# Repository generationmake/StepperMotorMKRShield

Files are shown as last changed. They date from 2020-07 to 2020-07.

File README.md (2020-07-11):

# StepperMotorMKRShield
StepperMotorMKRShield with Trinamic TMC5130A-TA drivers for two stepper motors compatible with Arduino MKR 

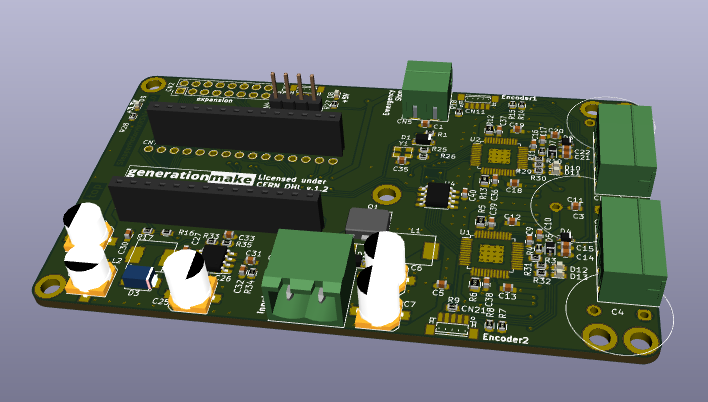
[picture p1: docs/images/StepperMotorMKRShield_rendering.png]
StepperMotorMKRShield rendering


## PCB

### Top

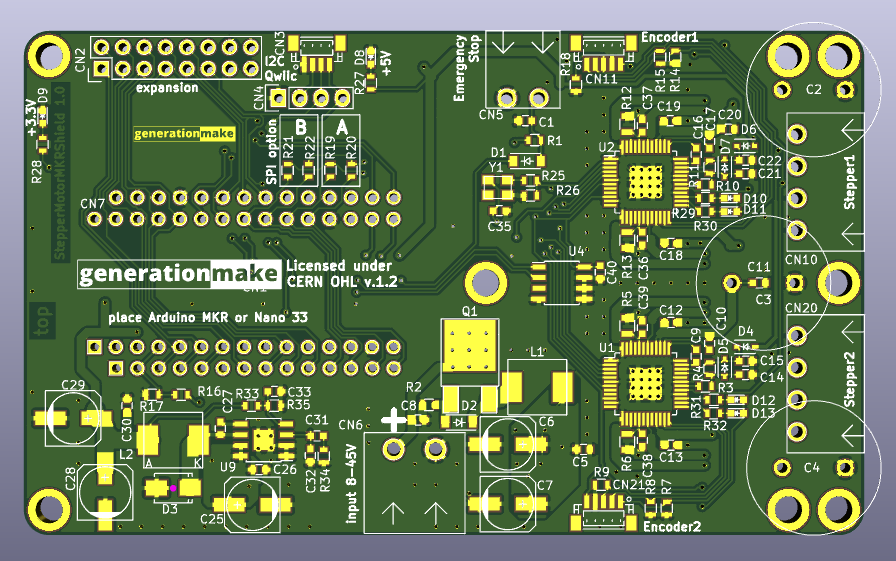
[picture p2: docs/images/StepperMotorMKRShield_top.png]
StepperMotorMKRShield PCB top


### Bottom

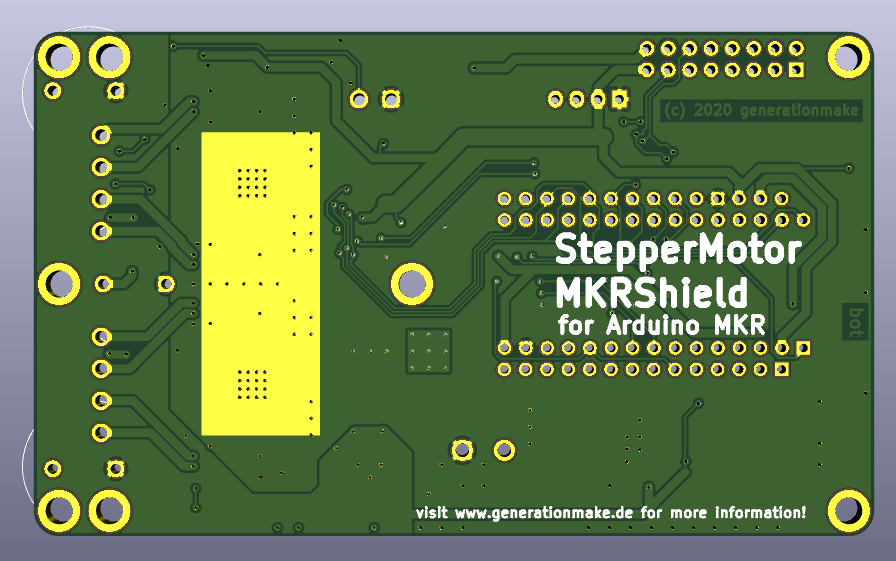
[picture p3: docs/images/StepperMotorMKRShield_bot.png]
StepperMotorMKRShield PCB bot


## License

This hardware is licensed under the CERN OHL v. 1.2

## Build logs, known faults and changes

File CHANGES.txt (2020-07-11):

StepperMotorMKRShield - Stepper Motor driver feather wing for Arduino MKR
see full project documentation at https://github.com/generationmake/StepperMotorMKRShield

changes

version 1.0 - 2020-07-12
* initial release

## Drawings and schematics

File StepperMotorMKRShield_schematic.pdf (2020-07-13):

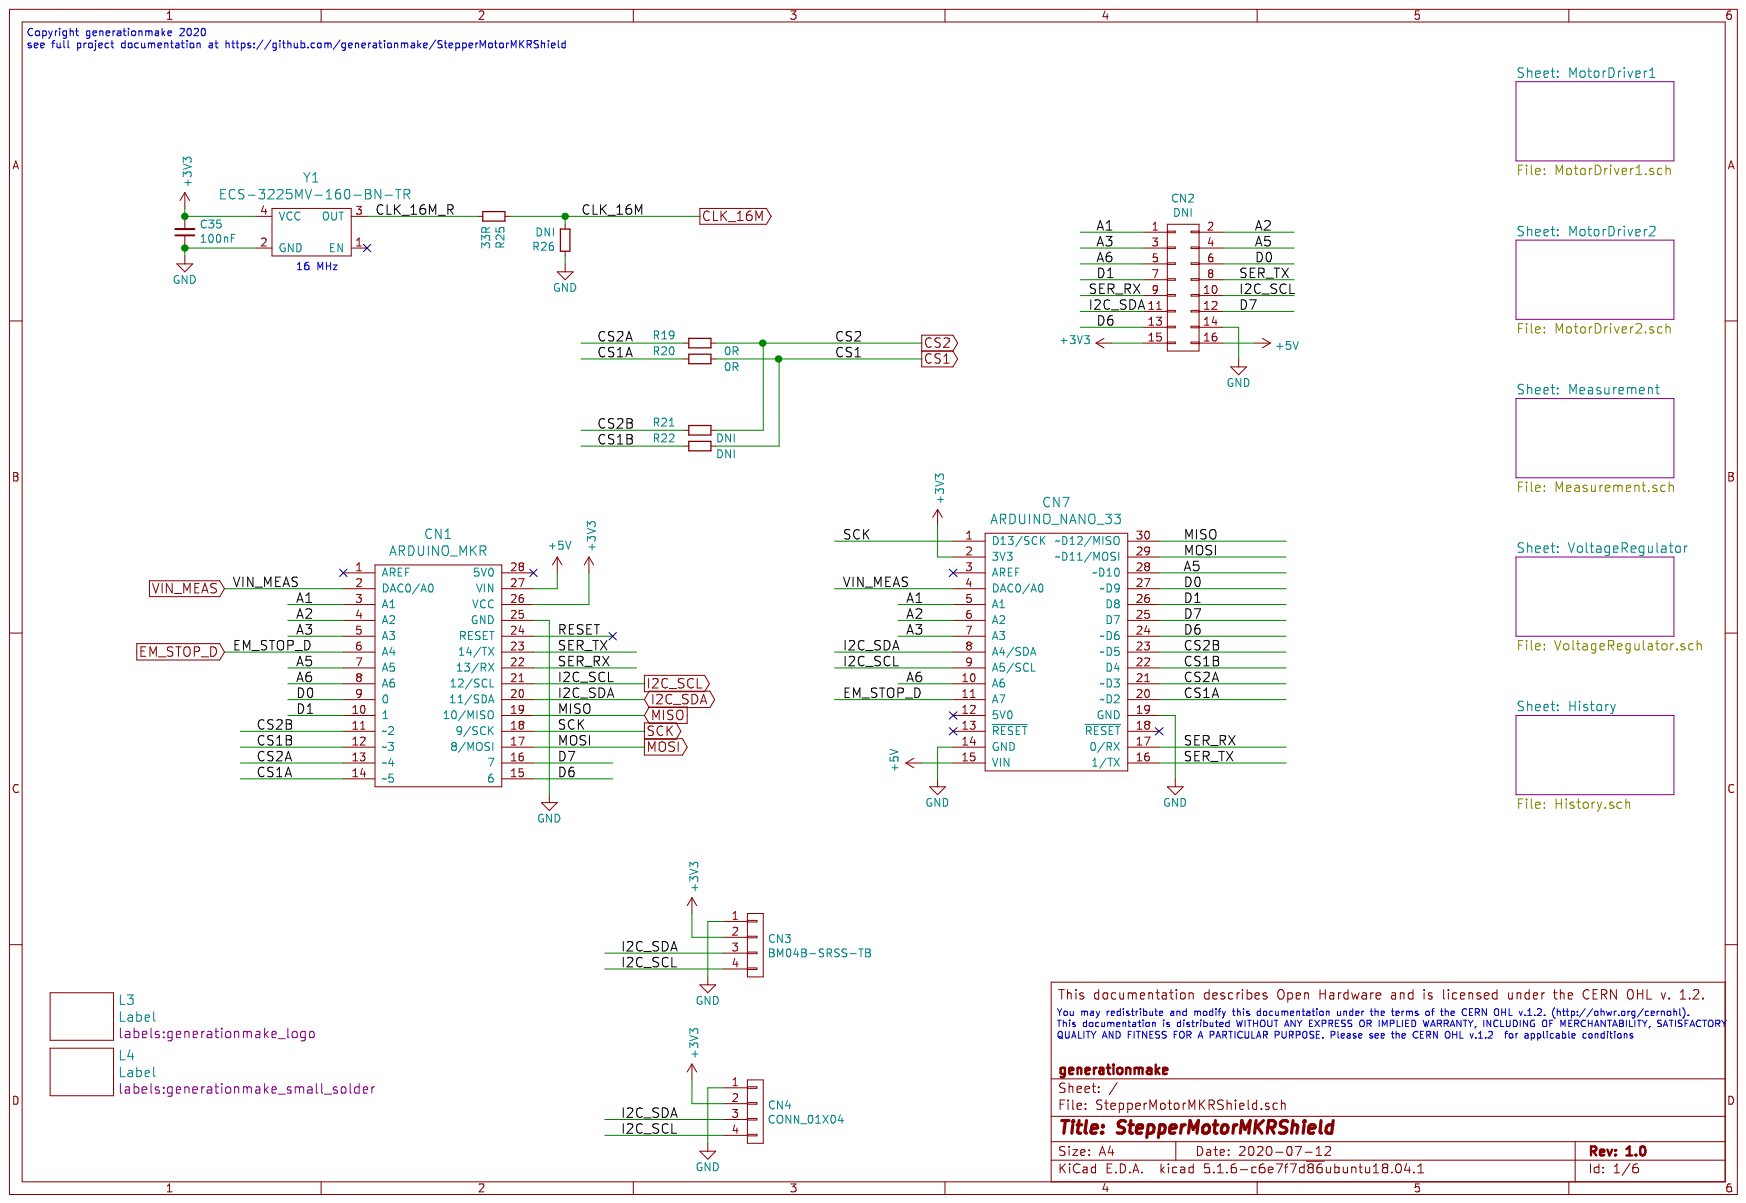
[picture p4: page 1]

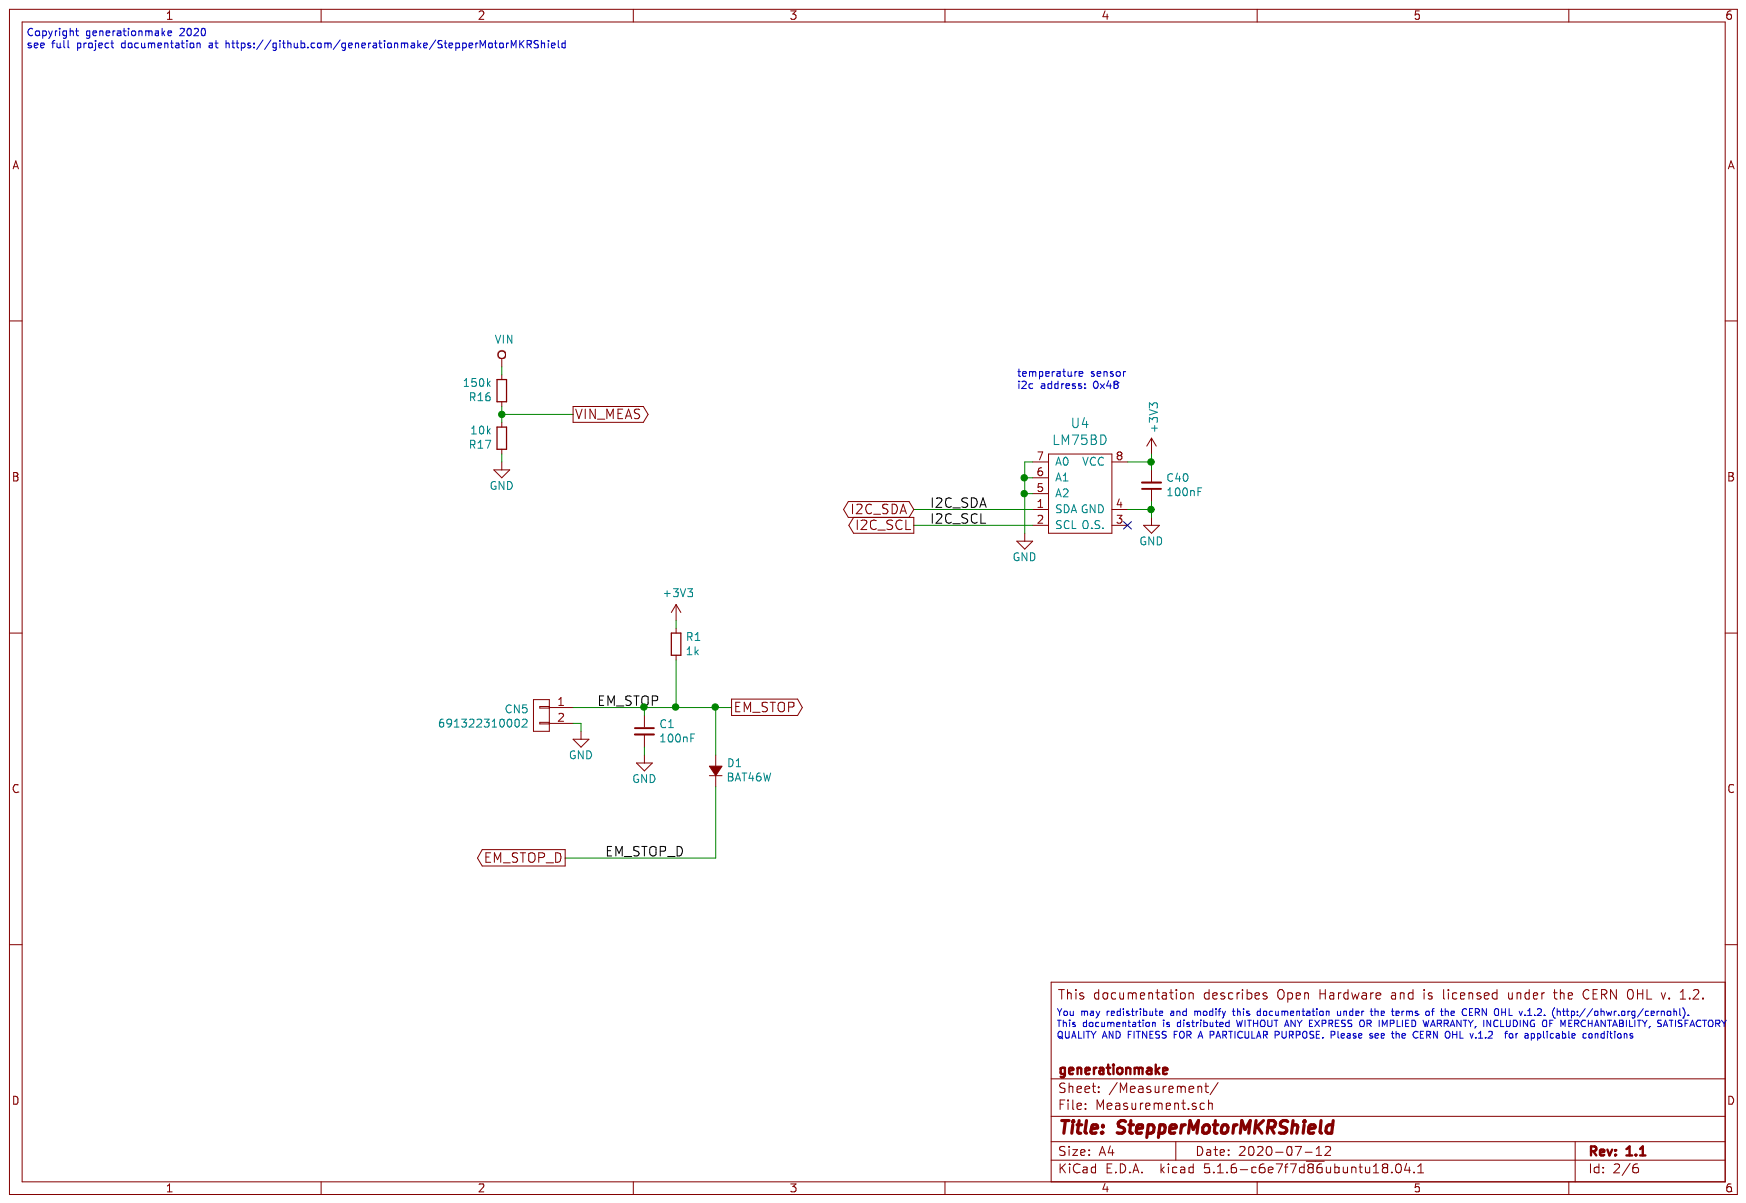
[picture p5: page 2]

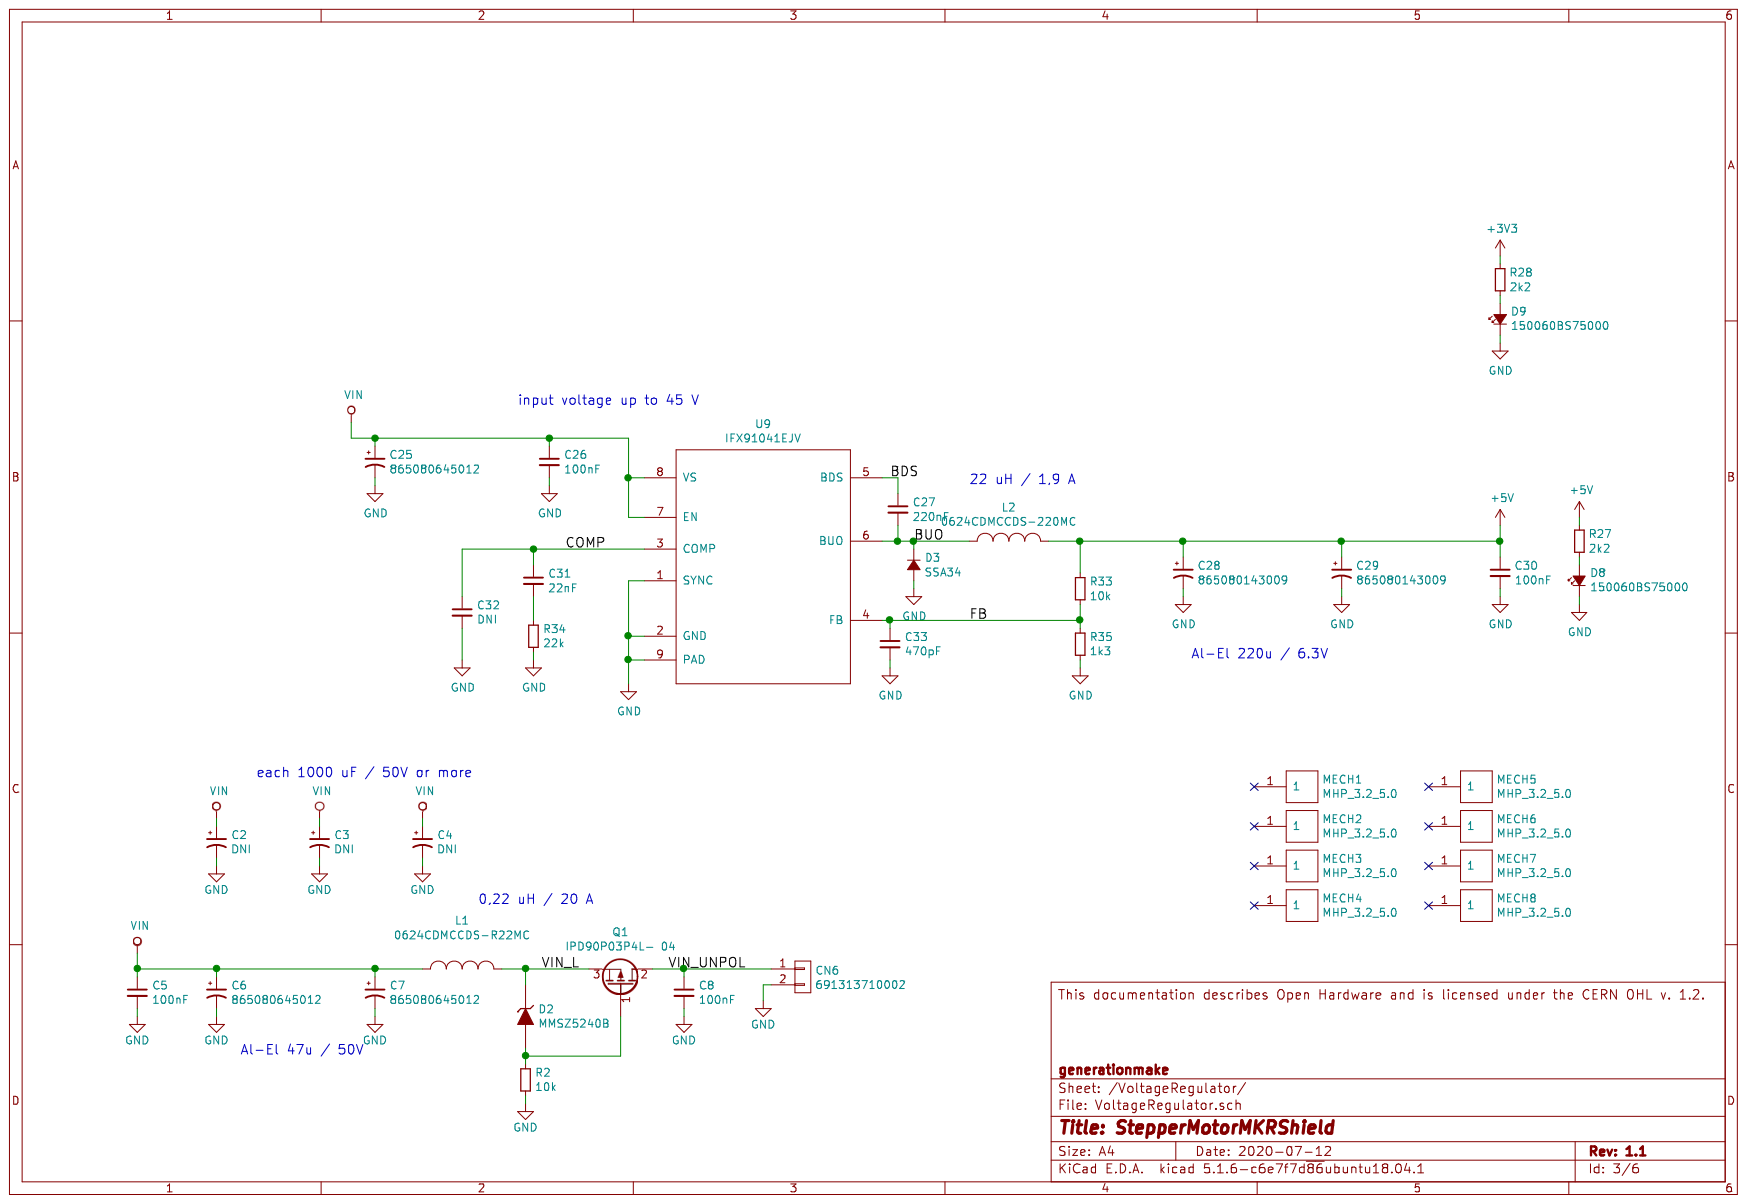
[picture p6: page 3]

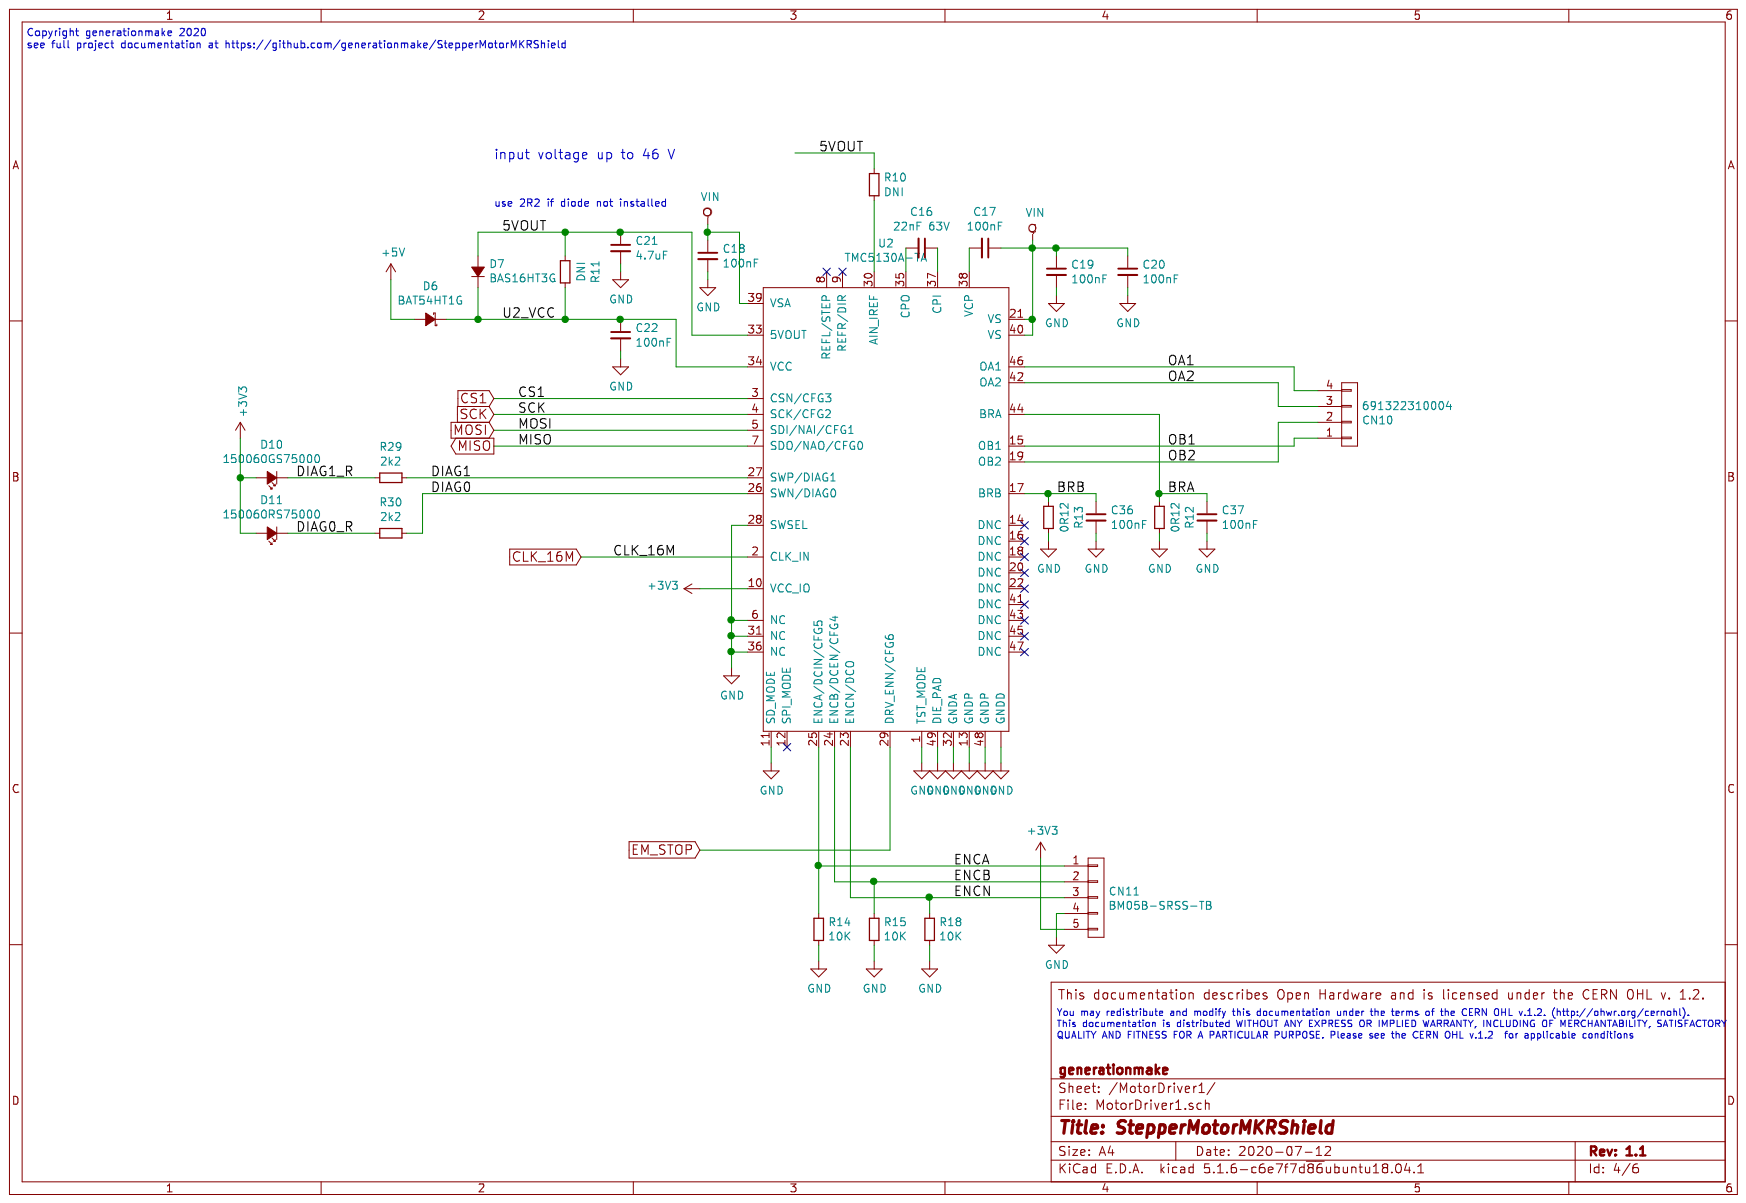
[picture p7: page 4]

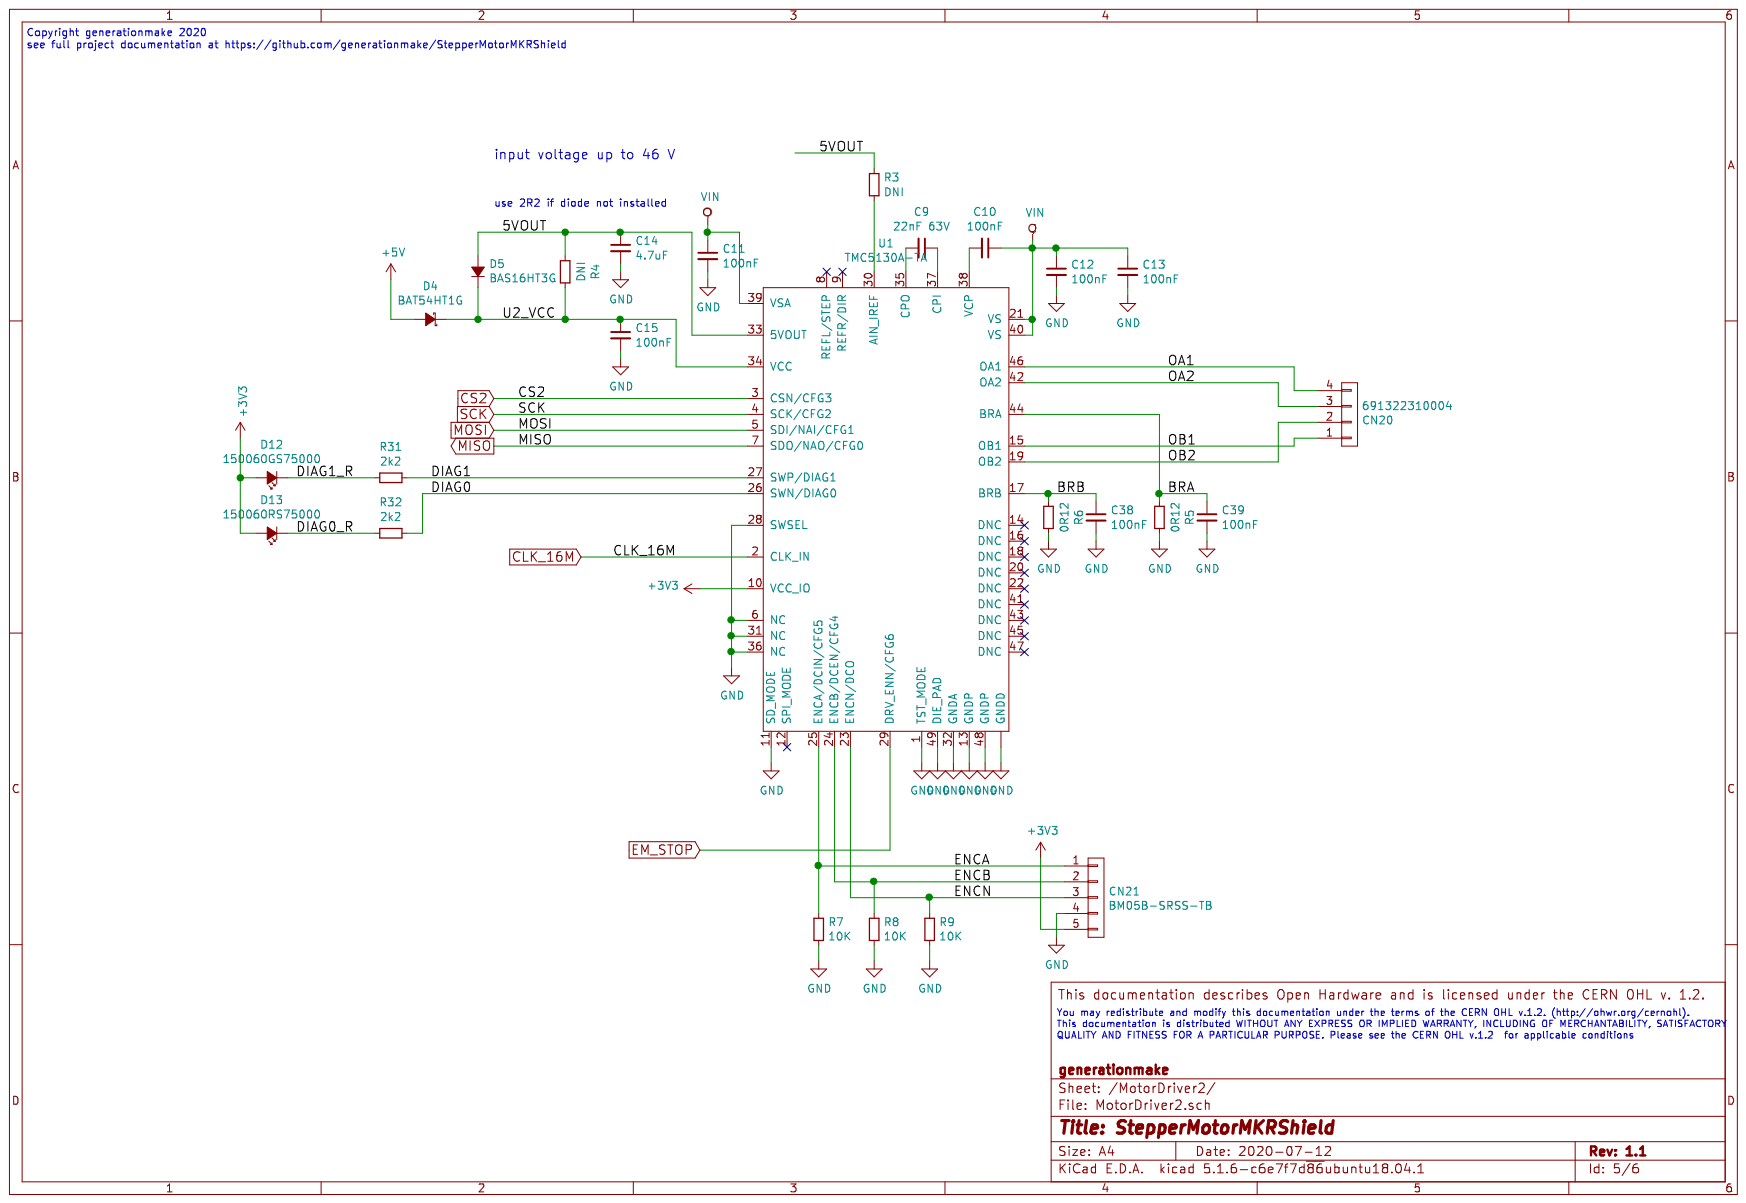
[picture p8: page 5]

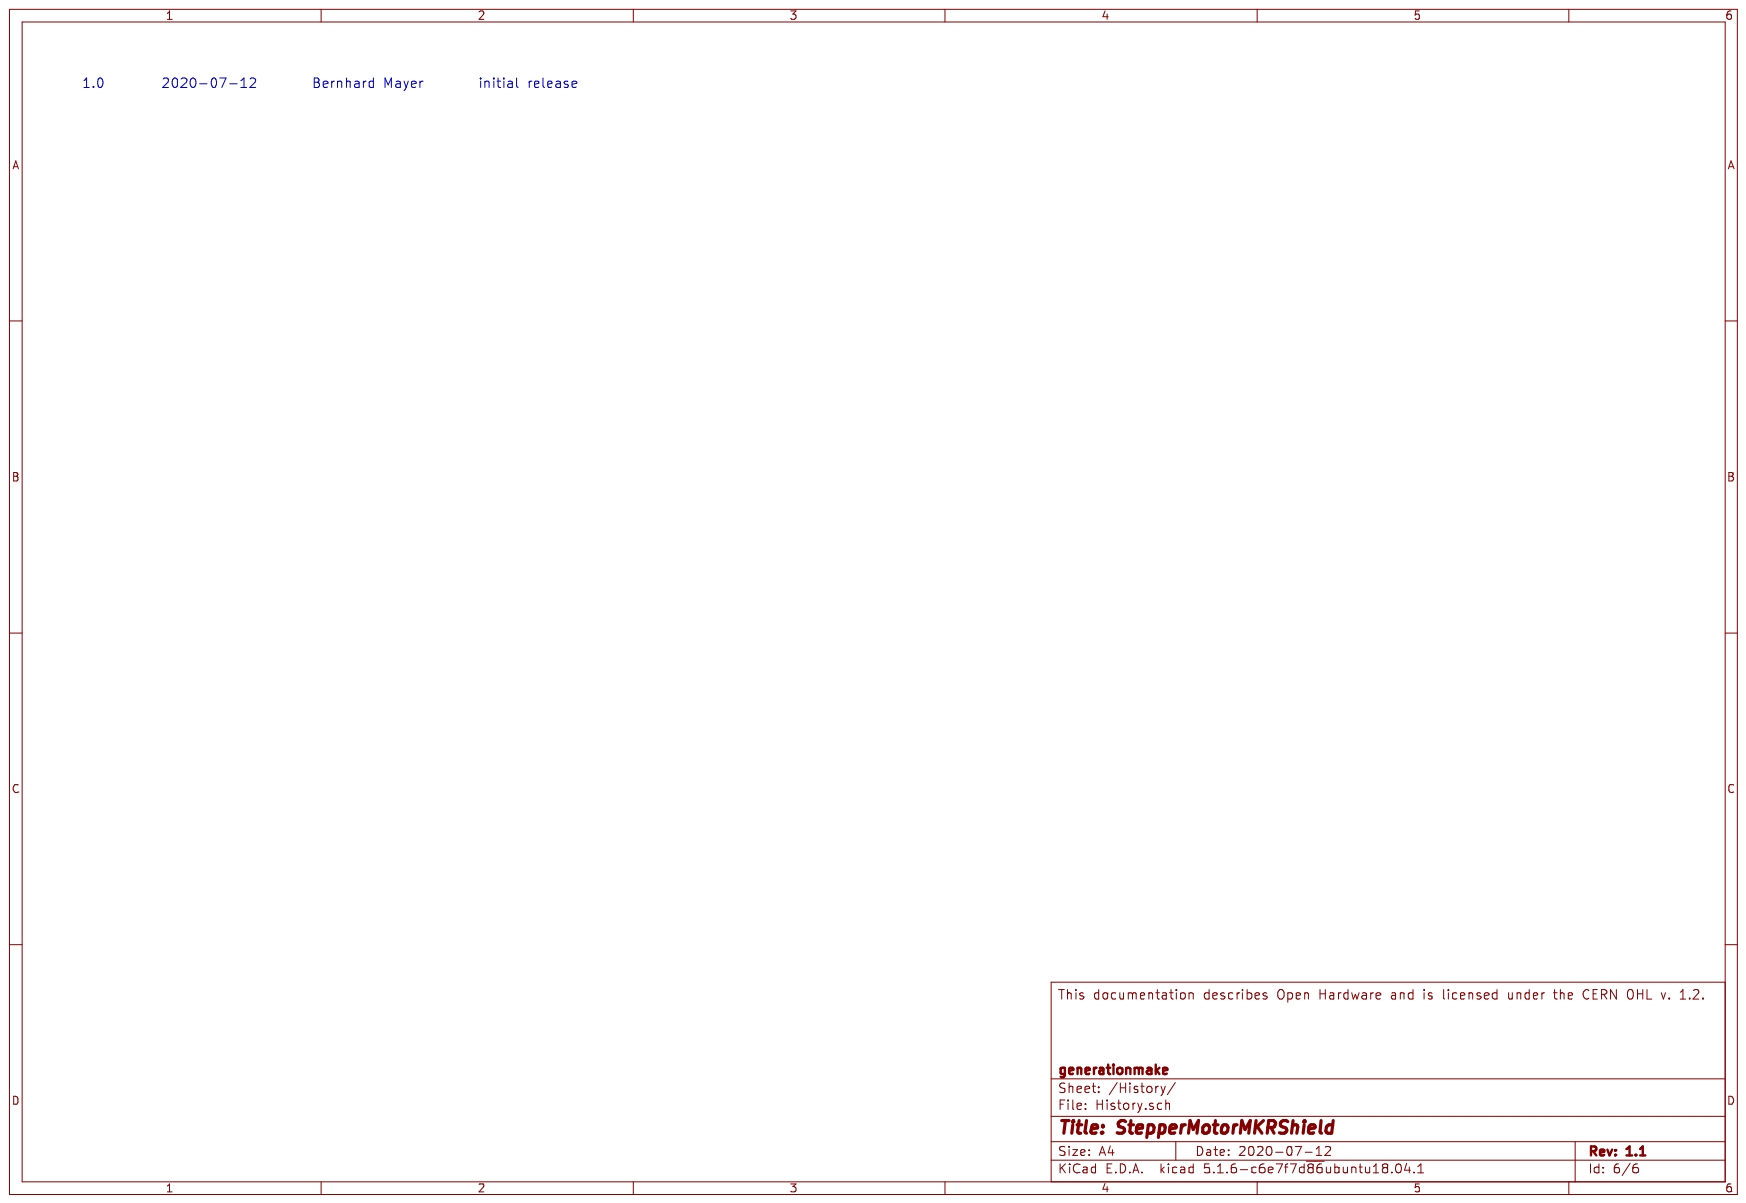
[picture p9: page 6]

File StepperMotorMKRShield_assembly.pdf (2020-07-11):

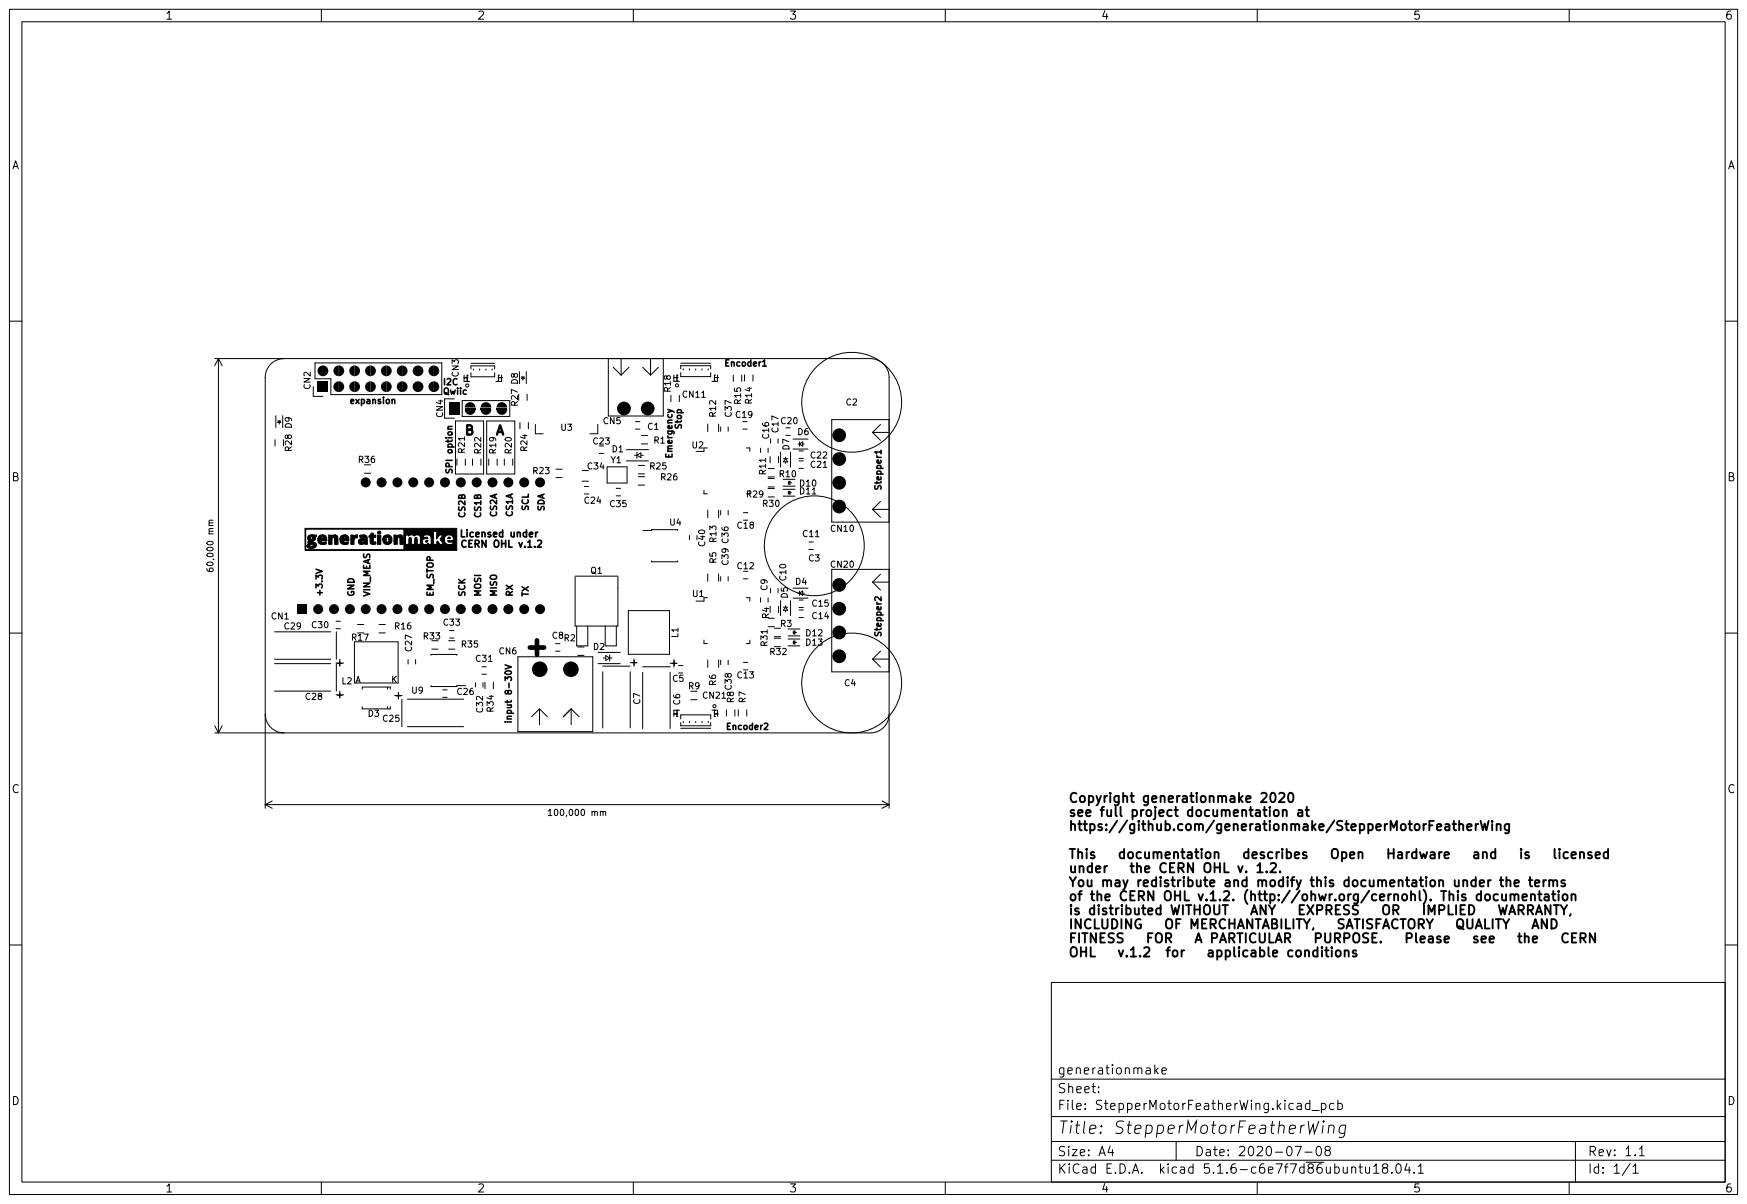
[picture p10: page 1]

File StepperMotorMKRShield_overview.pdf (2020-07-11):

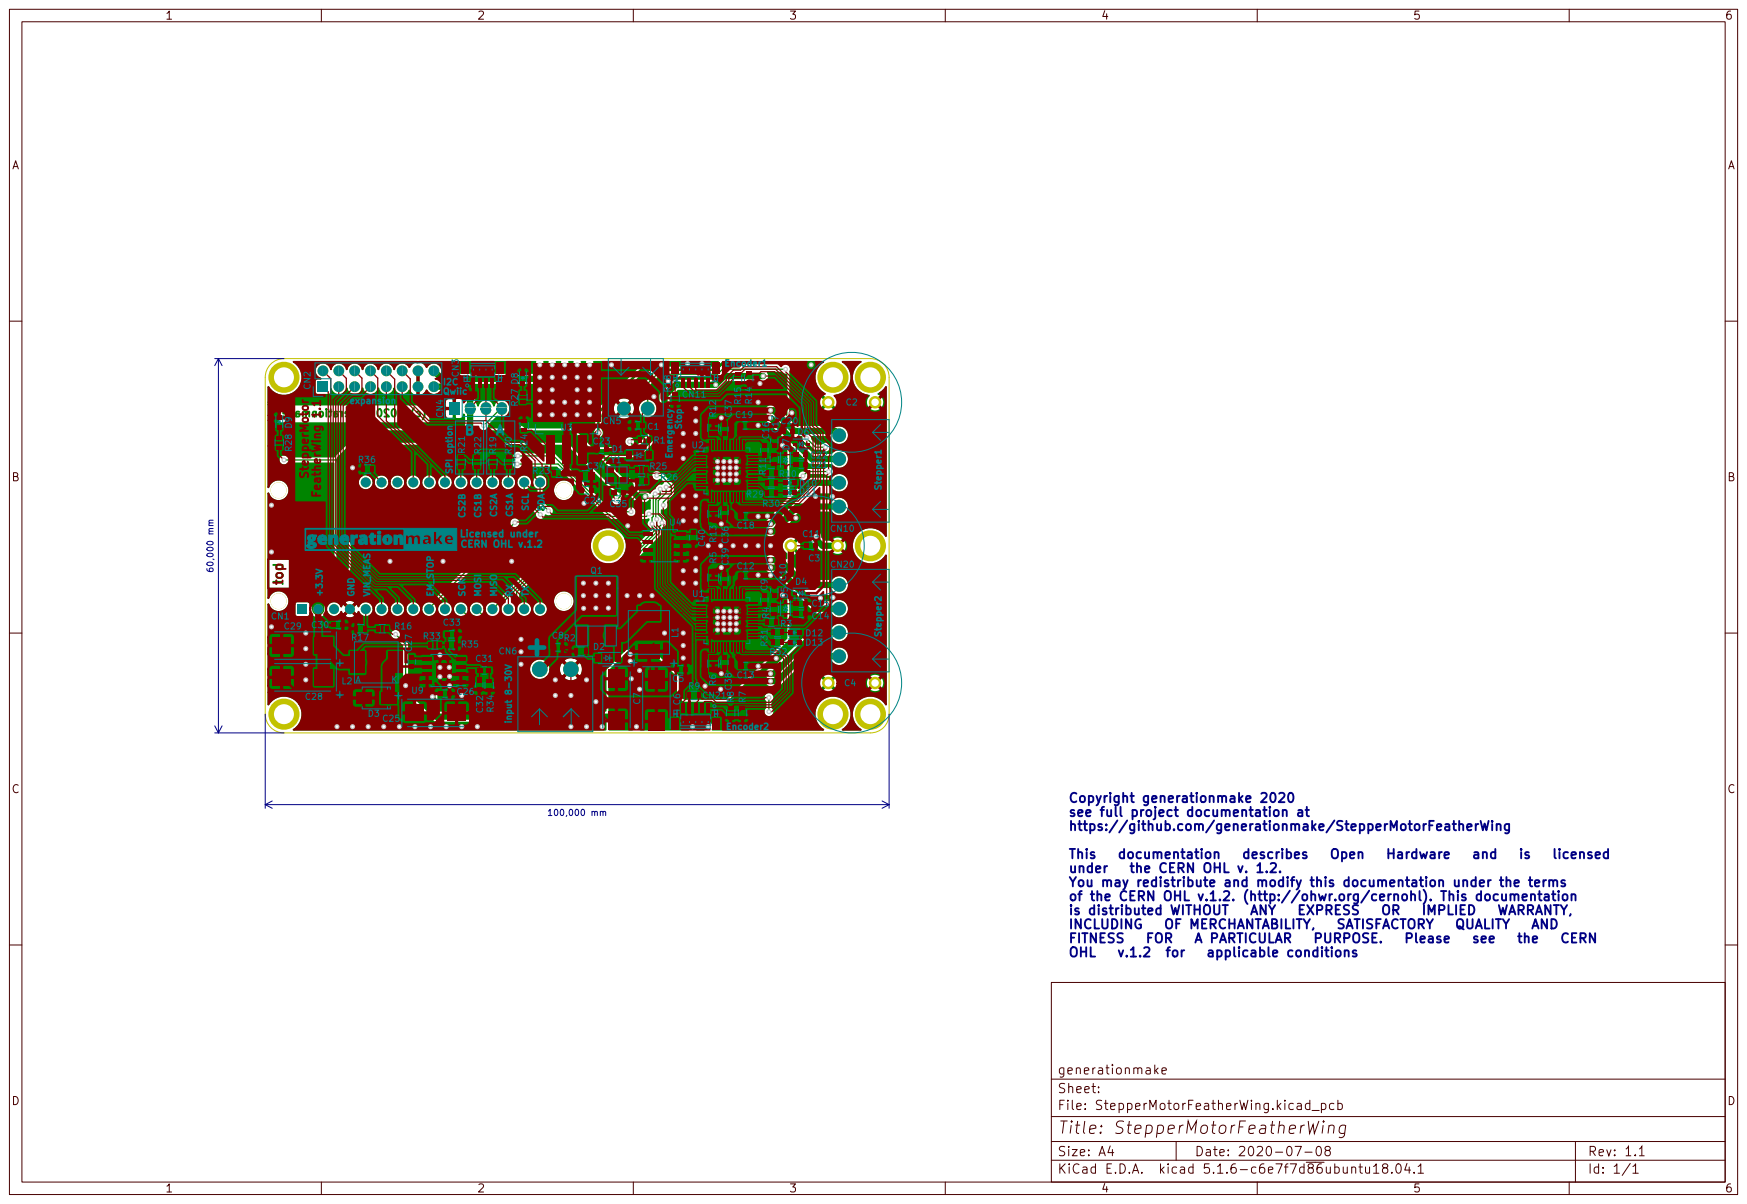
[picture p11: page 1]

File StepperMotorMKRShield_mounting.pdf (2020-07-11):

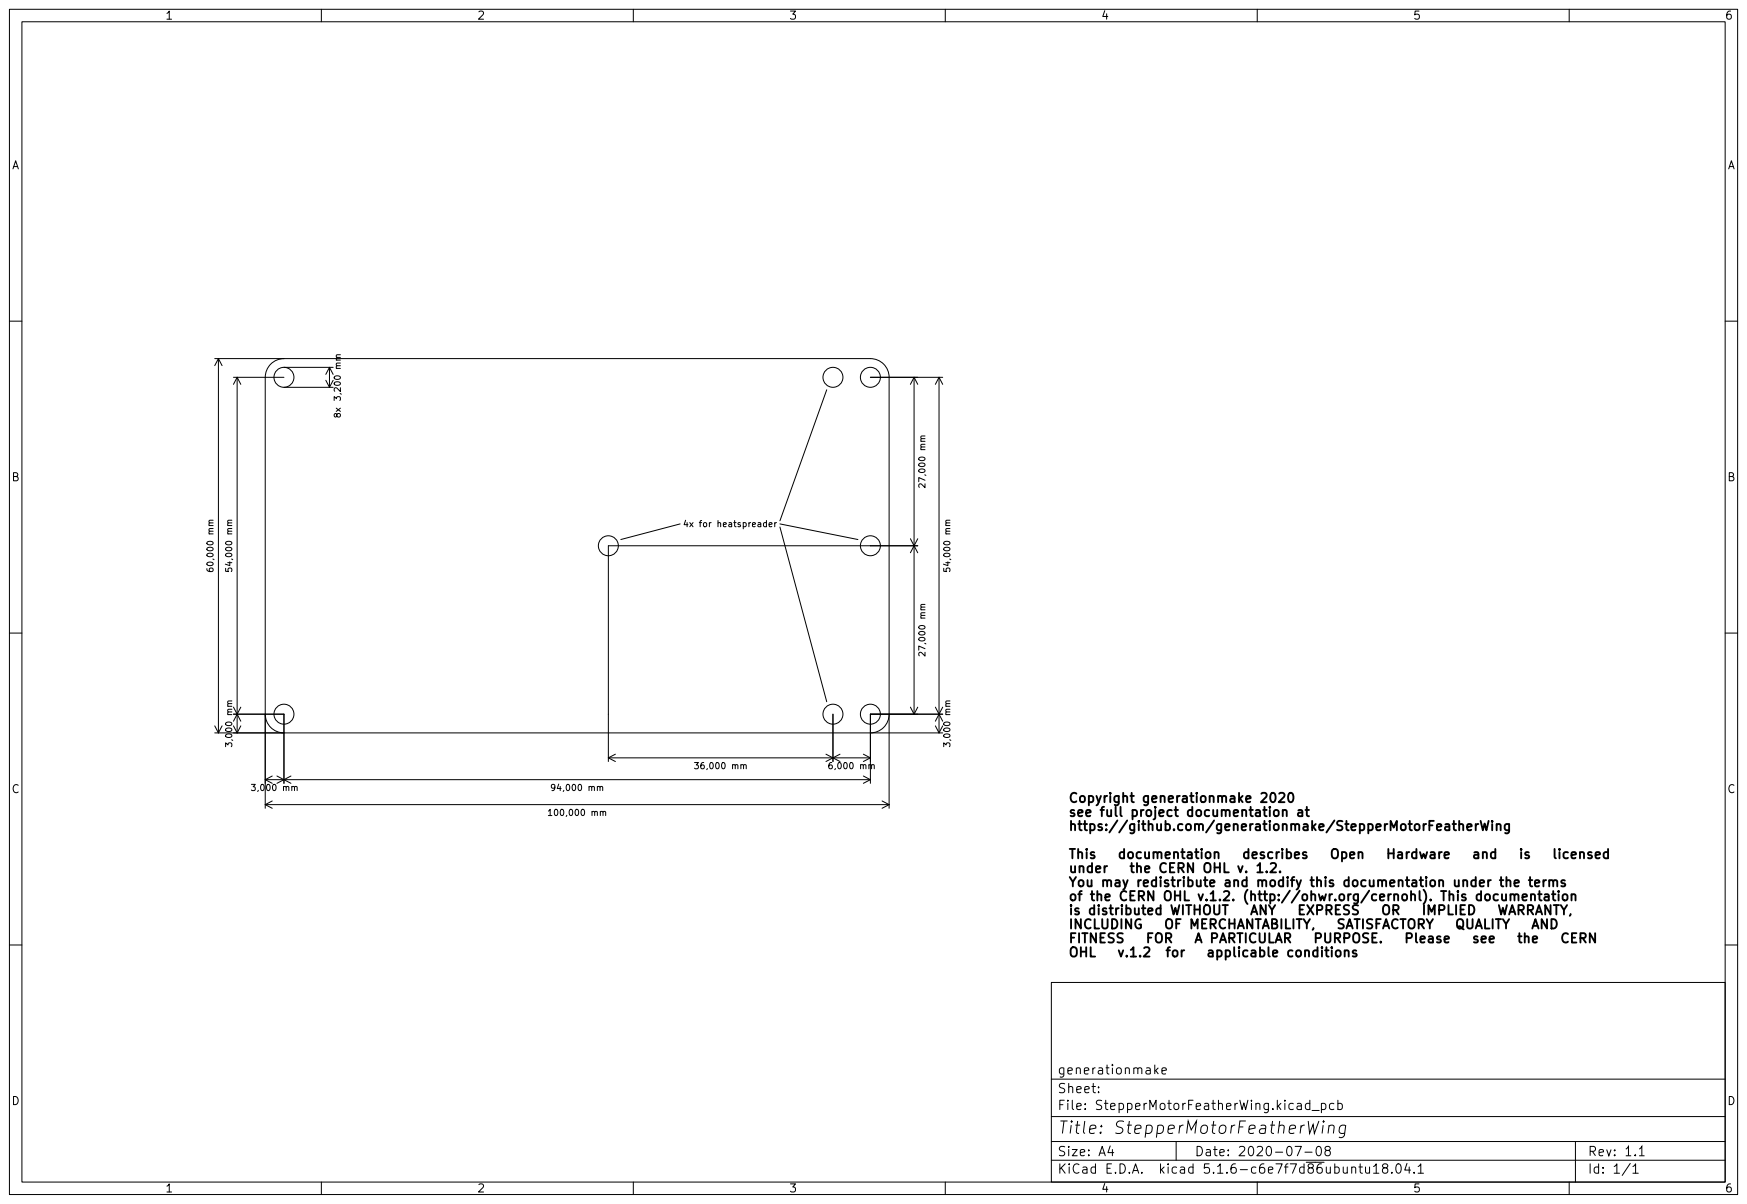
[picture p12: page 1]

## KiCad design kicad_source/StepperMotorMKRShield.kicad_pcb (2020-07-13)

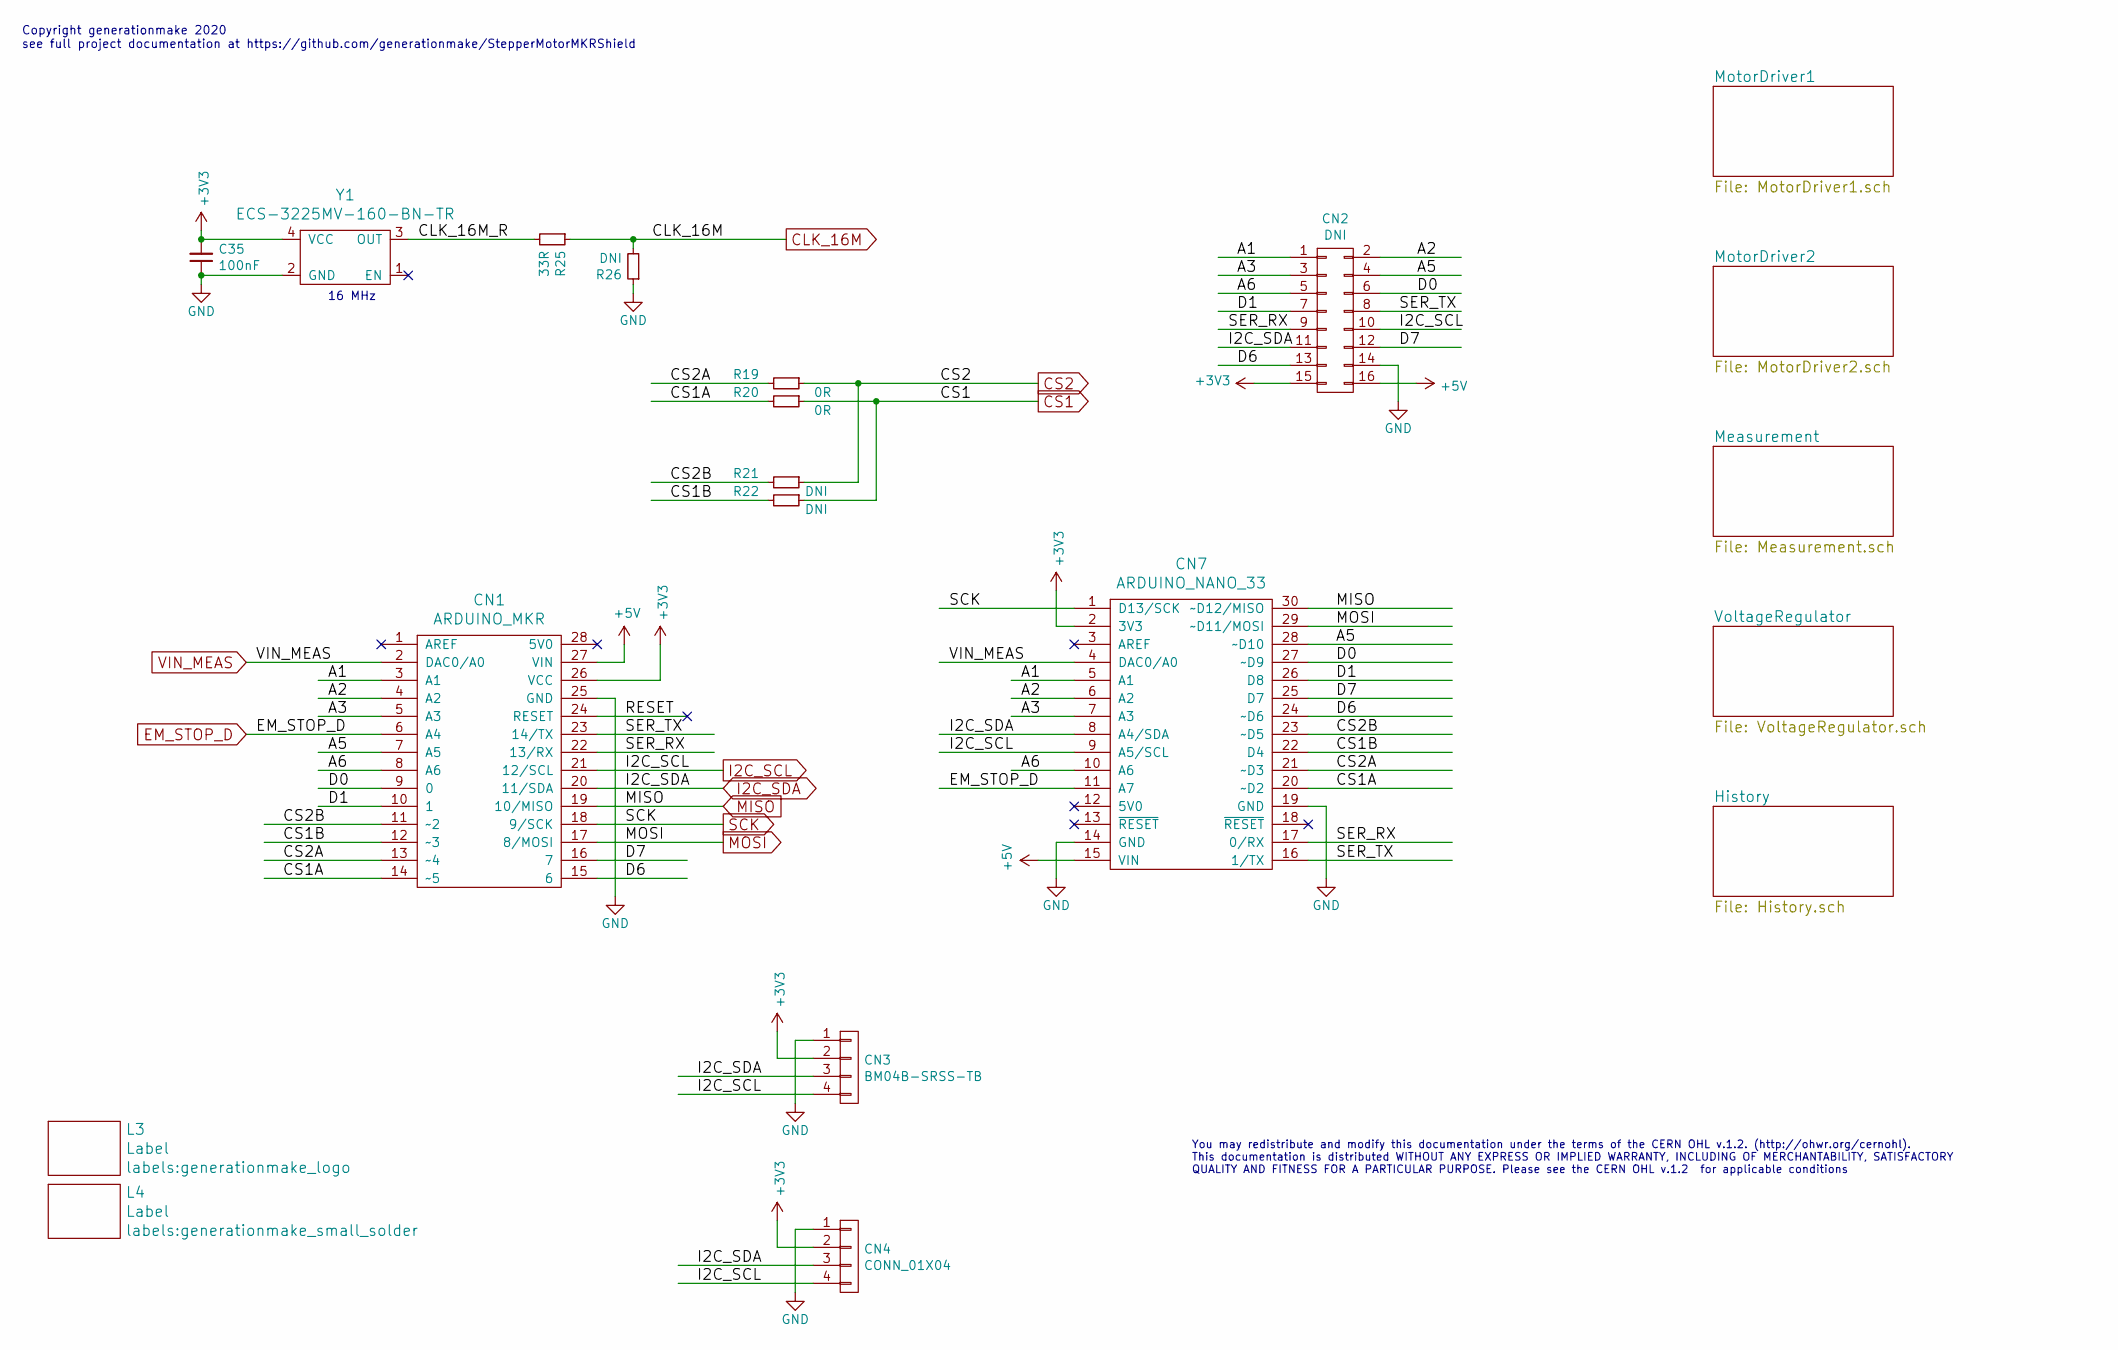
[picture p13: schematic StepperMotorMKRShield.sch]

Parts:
C35: 100nF; C_0603
CN1: ARDUINO_MKR; ARDUINO_MKR_BASEBOARD
CN2: DNI; Pin_Header_Straight_2x08
CN3: BM04B-SRSS-TB; Connectors_JST_BM04B-SRSS-TB
CN4: CONN_01X04; Pin_Header_Straight_1x04
CN7: ARDUINO_NANO_33
L3: Label; generationmake_logo
L4: Label; generationmake_small_solder
R19, R20: 0R; R_0603
R21, R22, R26: DNI; R_0603
R25: 33R; R_0603
Y1: ECS-3225MV-160-BN-TR; Crystal_SMD_3.2x2.5mm_4Pad

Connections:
+3V3: C35.2, CN1.26 (VCC), CN2.15, CN3.2, CN4.2, CN7.2 (3V3), Y1.4 (VCC); also elsewhere on the board
+5V: CN1.27 (VIN), CN2.16, CN7.15 (VIN); also elsewhere on the board
/A1: CN1.3 (A1), CN2.1, CN7.5 (A1)
/A2: CN1.4 (A2), CN2.2, CN7.6 (A2)
/A3: CN1.5 (A3), CN2.3, CN7.7 (A3)
/A5: CN1.7 (A5), CN2.4, CN7.28 (~~D10)
/A6: CN1.8 (A6), CN2.5, CN7.10 (A6)
/CLK_16M_R: R25.2, Y1.3 (OUT)
/CS1A: CN1.14 (~~5), CN7.20 (~~D2), R20.2
/CS1B: CN1.12 (~~3), CN7.22 (D4), R22.2
/CS2A: CN1.13 (~~4), CN7.21 (~~D3), R19.2
/CS2B: CN1.11 (~~2), CN7.23 (~~D5), R21.2
/D0: CN1.9 (0), CN2.6, CN7.27 (~~D9)
/D1: CN1.10 (1), CN2.7, CN7.26 (D8)
/D6: CN1.15 (6), CN2.13, CN7.24 (~~D6)
/D7: CN1.16 (7), CN2.12, CN7.25 (D7)
/SER_RX: CN1.22 (13/RX), CN2.9, CN7.17 (0/RX)
/SER_TX: CN1.23 (14/TX), CN2.8, CN7.16 (1/TX)
CLK_16M: R25.1, R26.2; also elsewhere on the board
CS1: R20.1, R22.1; also elsewhere on the board
CS2: R19.1, R21.1; also elsewhere on the board
EM_STOP_D: CN1.6 (A4), CN7.11 (A7); also elsewhere on the board
GND: C35.1, CN1.25 (GND), CN2.14, CN3.1, CN4.1, CN7.14 (GND), CN7.19 (GND), R26.1, Y1.2 (GND); also elsewhere on the board
I2C_SCL: CN1.21 (12/SCL), CN2.10, CN3.4, CN4.4, CN7.9 (A5/SCL); also elsewhere on the board
I2C_SDA: CN1.20 (11/SDA), CN2.11, CN3.3, CN4.3, CN7.8 (A4/SDA); also elsewhere on the board
MISO: CN1.19 (10/MISO), CN7.30 (~~D12/MISO); also elsewhere on the board
MOSI: CN1.17 (8/MOSI), CN7.29 (~~D11/MOSI); also elsewhere on the board
SCK: CN1.18 (9/SCK), CN7.1 (D13/SCK); also elsewhere on the board
VIN_MEAS: CN1.2 (DAC0/A0), CN7.4 (DAC0/A0); also elsewhere on the board

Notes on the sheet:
Copyright generationmake 2020 see full project documentation at https://github.com/generationmake/StepperMotorMKRShield
You may redistribute and modify this documentation under the terms of the CERN OHL v.1.2. (http://ohwr.org/cernohl). This documentation is distributed WITHOUT ANY EXPRESS OR IMPLIED WARRANTY, INCLUDING OF MERCHANTABILITY, SATISFACTORY QUALITY AND FITNESS FOR A PARTICULAR PURPOSE. Please see the CER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
16 MHz

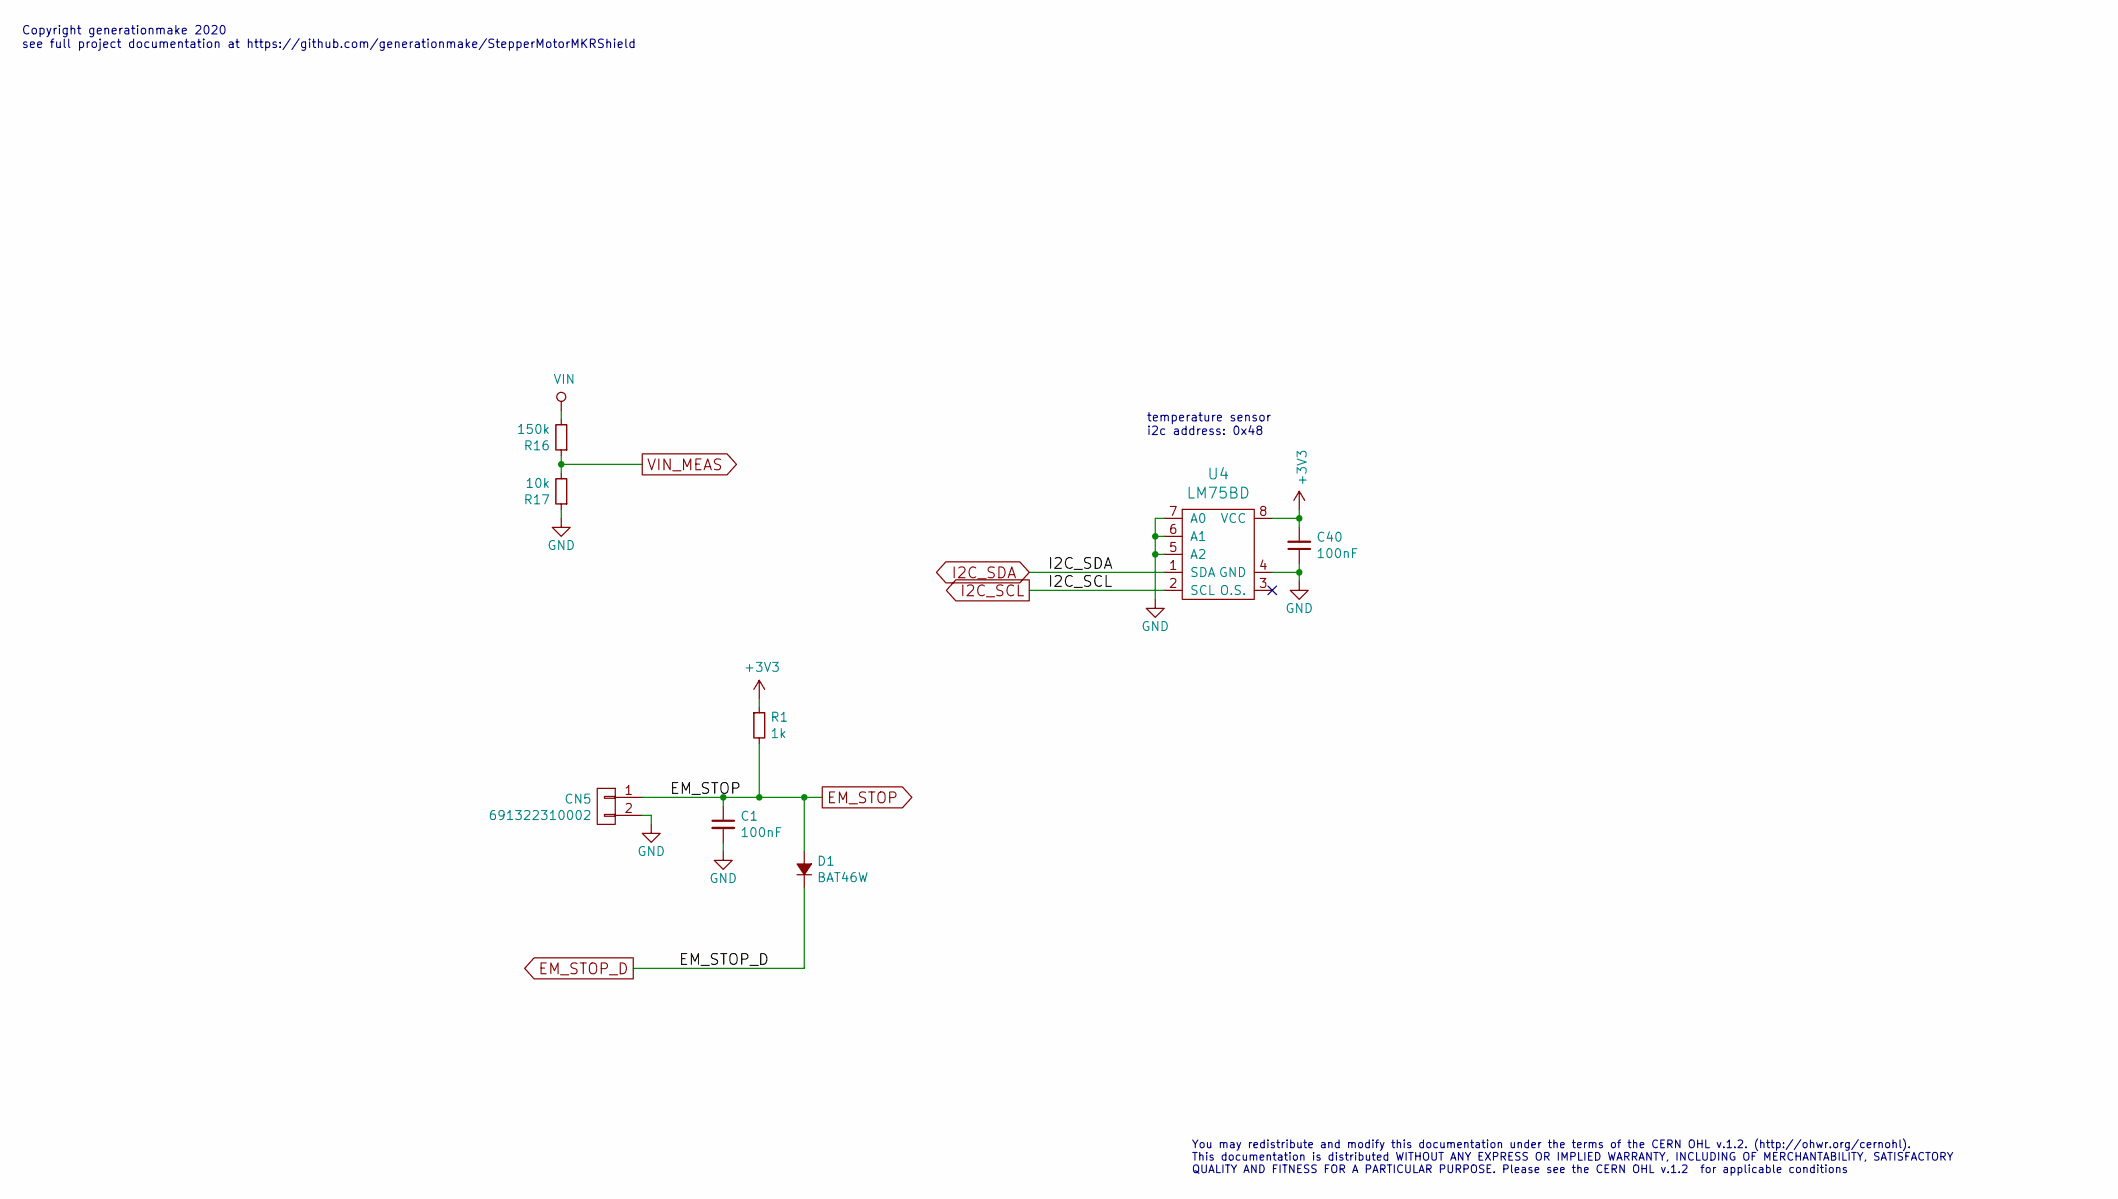
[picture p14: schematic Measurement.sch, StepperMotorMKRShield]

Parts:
C1, C40: 100nF; C_0603
CN5: 691322310002; WR-TBL_691322310002
D1: BAT46W; SOD-123
R1: 1k; R_0603
R16: 150k; R_0603
R17: 10k; R_0603
U4: LM75BD; SOIC-8_3.9x4.9mm_Pitch1.27mm

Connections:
+3V3: C40.2, R1.1, U4.8 (VCC); also elsewhere on the board
EM_STOP: C1.1, CN5.1, D1.2 (A), R1.2; also elsewhere on the board
EM_STOP_D: D1.1 (K); also elsewhere on the board
GND: C1.2, C40.1, CN5.2, R17.1, U4.4 (GND), U4.5 (A2), U4.6 (A1), U4.7 (A0); also elsewhere on the board
I2C_SCL: U4.2 (SCL); also elsewhere on the board
I2C_SDA: U4.1 (SDA); also elsewhere on the board
VIN: R16.2; also elsewhere on the board
VIN_MEAS: R16.1, R17.2; also elsewhere on the board

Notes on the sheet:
Copyright generationmake 2020 see full project documentation at https://github.com/generationmake/StepperMotorMKRShield
You may redistribute and modify this documentation under the terms of the CERN OHL v.1.2. (http://ohwr.org/cernohl). This documentation is distributed WITHOUT ANY EXPRESS OR IMPLIED WARRANTY, INCLUDING OF MERCHANTABILITY, SATISFACTORY QUALITY AND FITNESS FOR A PARTICULAR PURPOSE. Please see the CER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
temperature sensor i2c address: 0x48

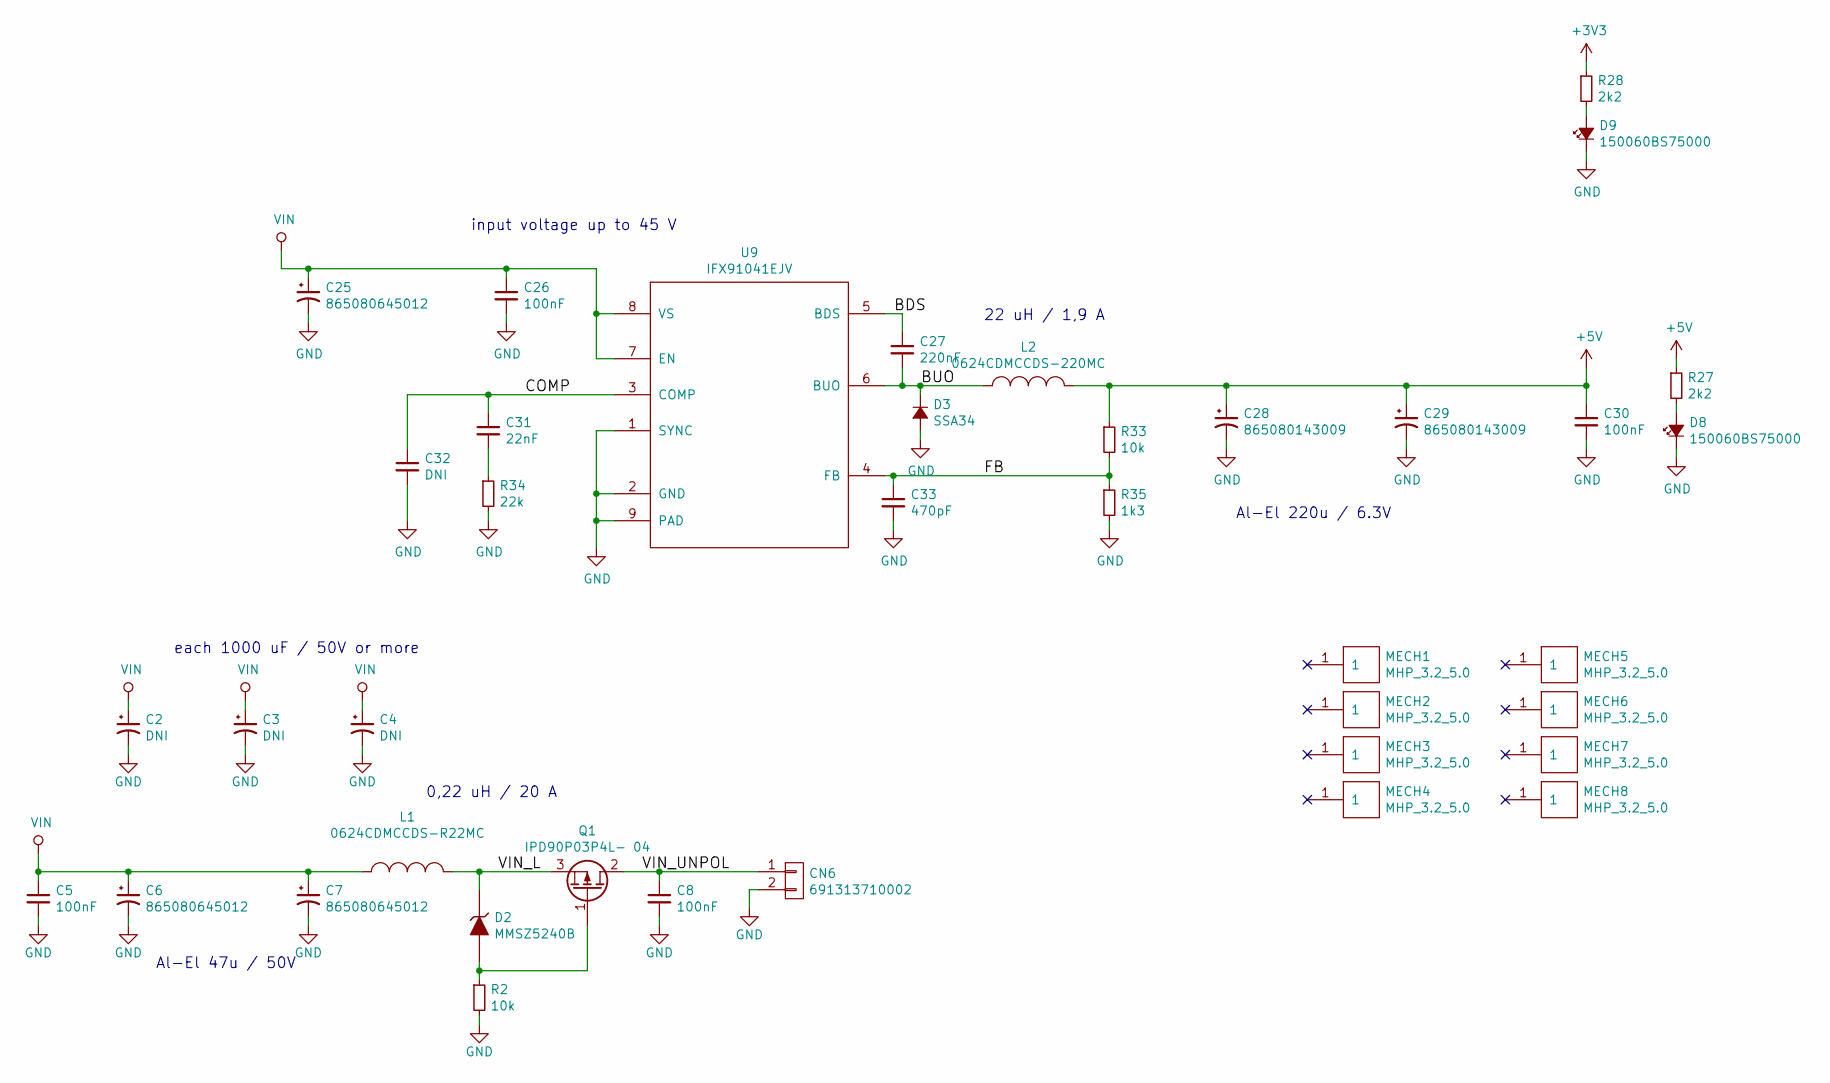
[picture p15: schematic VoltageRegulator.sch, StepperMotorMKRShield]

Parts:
C2, C3, C4: DNI; C_elec_THT_16x25_RM7.5
C5, C8, C26, C30: 100nF; C_0603
C6, C7, C25: 865080645012; c_elec_6.3x7.7
C27: 220nF; C_0603
C28, C29: 865080143009; c_elec_6.3x5.7
C31: 22nF; C_0603
C32: DNI; C_0603
C33: 470pF; C_0603
CN6: 691313710002; WR-TBL_691313710002
D2: MMSZ5240B; SOD-123
D3: SSA34; SMA_Standard
D8, D9: 150060BS75000; LED_0603
L1: 0624CDMCCDS-R22MC; Sumida-0624CDMCCDS
L2: 0624CDMCCDS-220MC; Sumida-0624CDMCCDS
MECH1, MECH2, MECH3, MECH4, MECH5, MECH6, MECH7, MECH8: MHP_3.2_5.0
Q1: IPD90P03P4L- 04; TO-252-2Lead
R2, R33: 10k; R_0603
R27, R28: 2k2; R_0603
R34: 22k; R_0603
R35: 1k3; R_0603
U9: IFX91041EJV; SOIC-8-1EP_3.9x4.9mm_Pitch1.27mm

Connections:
+3V3: R28.1; also elsewhere on the board
+5V: C28.1, C29.1, C30.1, L2.2, R27.1, R33.1; also elsewhere on the board
/VoltageRegulator/BDS: C27.1, U9.5 (BDS)
/VoltageRegulator/BUO: C27.2, D3.1 (K), L2.1, U9.6 (BUO)
/VoltageRegulator/COMP: C31.1, C32.1, U9.3 (COMP)
/VoltageRegulator/FB: C33.1, R33.2, R35.1, U9.4 (FB)
/VoltageRegulator/VIN_L: D2.1 (K), L1.2, Q1.3 (S)
/VoltageRegulator/VIN_UNPOL: C8.1, CN6.1, Q1.2 (D)
GND: C2.2, C3.2, C4.2, C5.2, C6.2, C7.2, C8.2, C25.2, C26.2, C28.2, C29.2, C30.2, C32.2, C33.2, CN6.2, D3.2 (A), D8.1 (K), D9.1 (K), R2.2, R34.2, R35.2, U9.1 (SYNC), U9.2 (GND), U9.9 (PAD); also elsewhere on the board
unnamed: C31.2, R34.1
unnamed: D2.2 (A), Q1.1 (G), R2.1
unnamed: D8.2 (A), R27.2
unnamed: D9.2 (A), R28.2
VIN: C2.1, C3.1, C4.1, C5.1, C6.1, C7.1, C25.1, C26.1, L1.1, U9.7 (EN), U9.8 (VS); also elsewhere on the board

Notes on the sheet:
input voltage up to 45 V
0,22 uH / 20 A
22 uH / 1,9 A
each 1000 uF / 50V or more
Al-El 47u / 50V
Al-El 220u / 6.3V

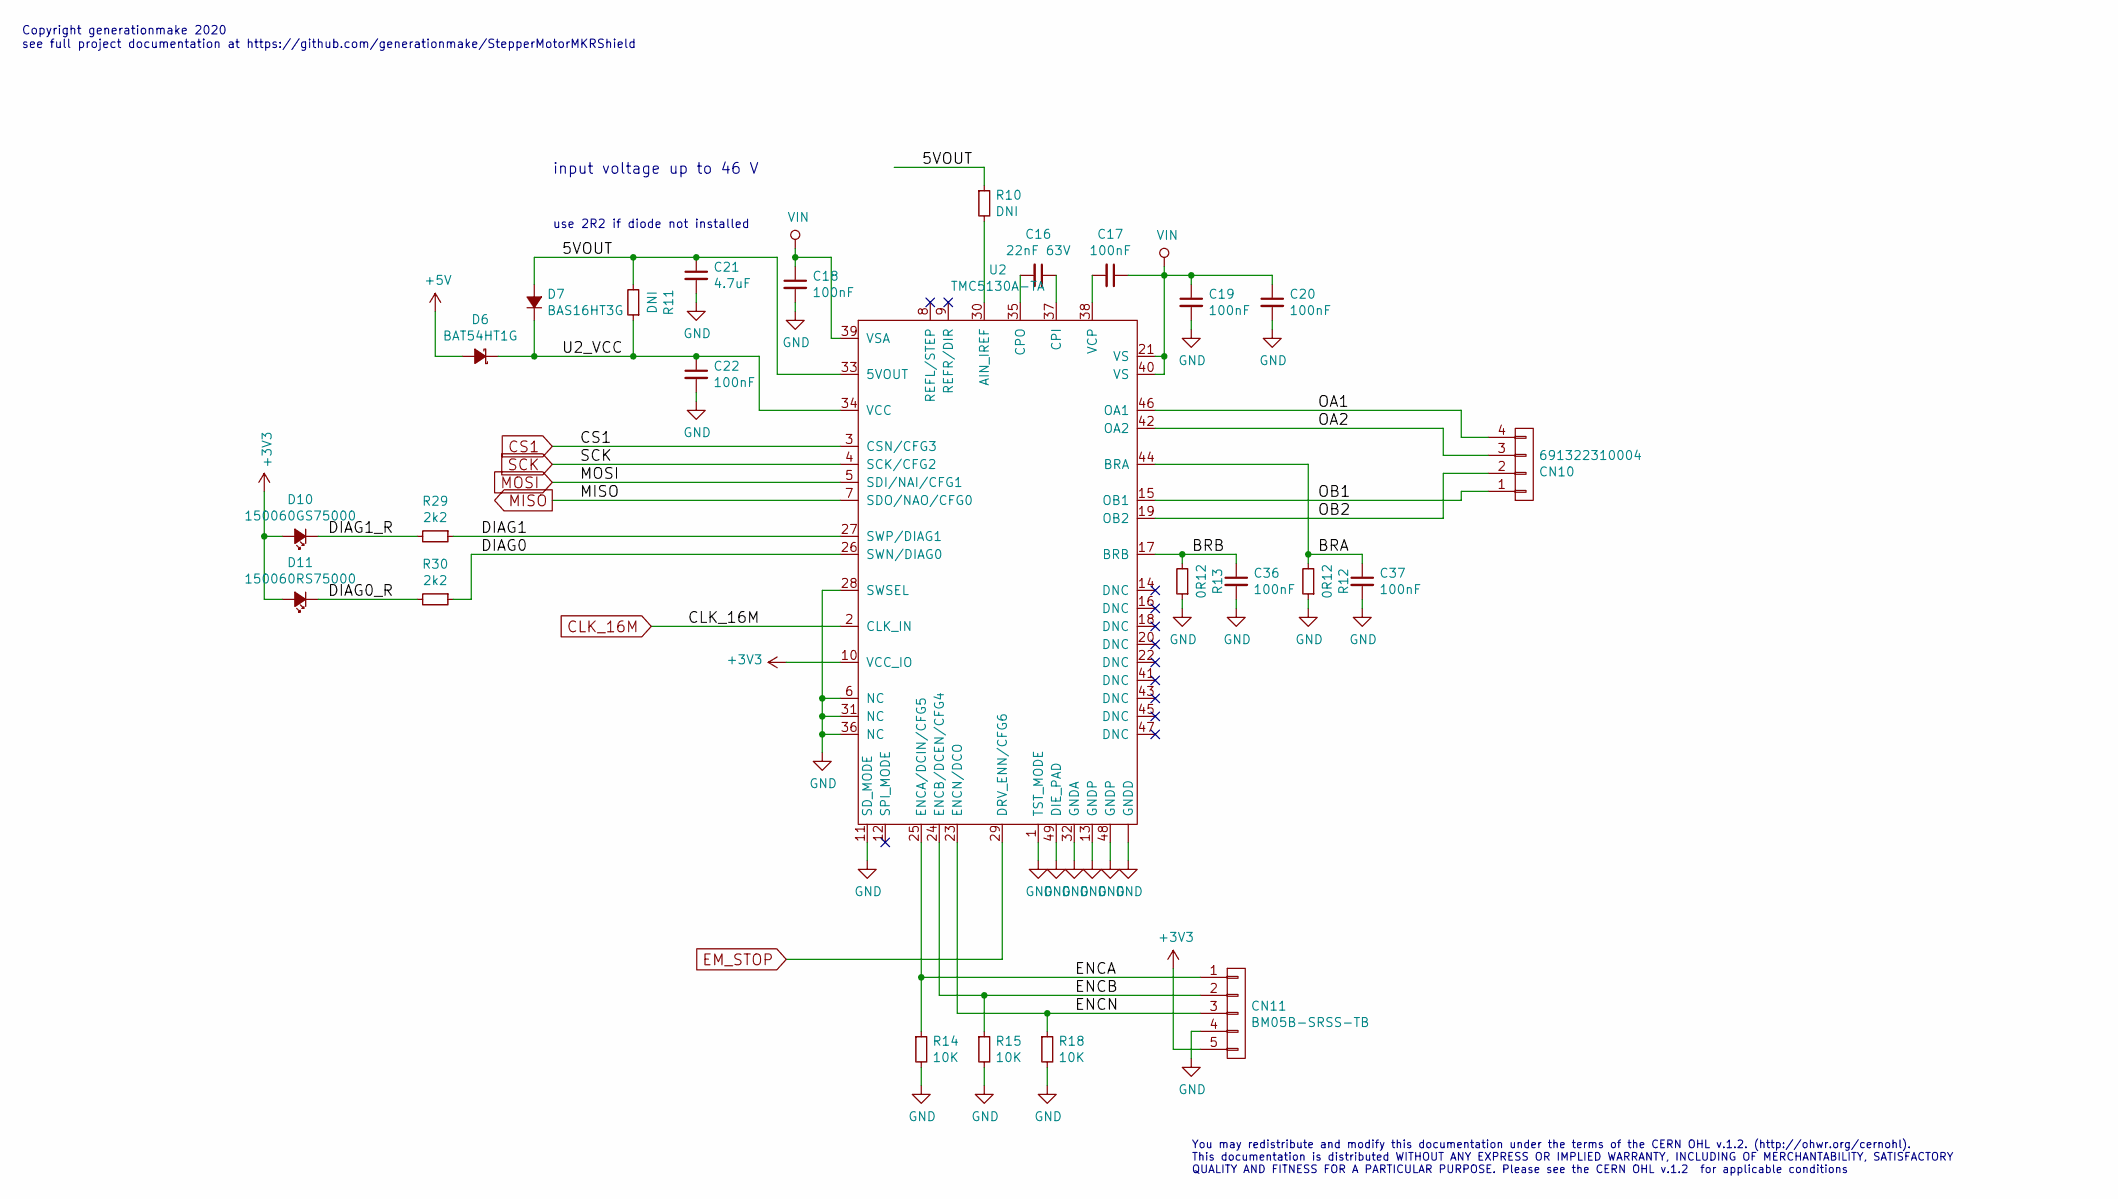
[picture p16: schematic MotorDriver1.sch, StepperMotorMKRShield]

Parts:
C16: 22nF 63V; C_0603
C17, C18, C19, C20, C22, C36, C37: 100nF; C_0603
C21: 4.7uF; C_0603
CN10: 691322310004; WR-TBL_691322310004
CN11: BM05B-SRSS-TB; Connectors_JST_BM05B-SRSS-TB
D6: BAT54HT1G; SOD-323
D7: BAS16HT3G; SOD-323
D10: 150060GS75000; LED_0603
D11: 150060RS75000; LED_0603
R10, R11: DNI; R_0603
R12, R13: 0R12; R_0805
R14, R15, R18: 10K; R_0603
R29, R30: 2k2; R_0603
U2: TMC5130A-TA; TQFP-48-1EP_7x7mm_Pitch0.5mm

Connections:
+3V3: CN11.5, D10.2 (A), D11.2 (A), U2.10 (VCC_IO); also elsewhere on the board
+5V: D6.2 (A); also elsewhere on the board
/MotorDriver1/5VOUT: C21.1, D7.2 (A), R10.1, R11.2, U2.33 (5VOUT)
/MotorDriver1/BRA: C37.1, R12.2, U2.44 (BRA)
/MotorDriver1/BRB: C36.1, R13.2, U2.17 (BRB)
/MotorDriver1/DIAG0: R30.1, U2.26 (SWN/DIAG0)
/MotorDriver1/DIAG0_R: D11.1 (K), R30.2
/MotorDriver1/DIAG1: R29.1, U2.27 (SWP/DIAG1)
/MotorDriver1/DIAG1_R: D10.1 (K), R29.2
/MotorDriver1/ENCA: CN11.1, R14.1, U2.25 (ENCA/DCIN/CFG5)
/MotorDriver1/ENCB: CN11.2, R15.1, U2.24 (ENCB/DCEN/CFG4)
/MotorDriver1/ENCN: CN11.3, R18.1, U2.23 (ENCN/DCO)
/MotorDriver1/OA1: CN10.4, U2.46 (OA1)
/MotorDriver1/OA2: CN10.3, U2.42 (OA2)
/MotorDriver1/OB1: CN10.1, U2.15 (OB1)
/MotorDriver1/OB2: CN10.2, U2.19 (OB2)
/MotorDriver1/U2_VCC: C22.1, D6.1 (K), D7.1 (K), R11.1, U2.34 (VCC)
CLK_16M: U2.2 (CLK_IN); also elsewhere on the board
CS1: U2.3 (CSN/CFG3); also elsewhere on the board
EM_STOP: U2.29 (DRV_ENN/CFG6); also elsewhere on the board
GND: C18.2, C19.2, C20.2, C21.2, C22.2, C36.2, C37.2, CN11.4, R12.1, R13.1, R14.2, R15.2, R18.2, U2.1 (TST_MODE), U2.6 (NC), U2.11 (SD_MODE), U2.13 (GNDP), U2.28 (SWSEL), U2.31 (NC), U2.32 (GNDA), U2.36 (NC), U2.48 (GNDP), U2.49 (DIE_PAD), U2.~ (GNDD); also elsewhere on the board
MISO: U2.7 (SDO/NAO/CFG0); also elsewhere on the board
MOSI: U2.5 (SDI/NAI/CFG1); also elsewhere on the board
unnamed: C16.1, U2.37 (CPI)
unnamed: C16.2, U2.35 (CPO)
unnamed: C17.2, U2.38 (VCP)
unnamed: R10.2, U2.30 (AIN_IREF)
SCK: U2.4 (SCK/CFG2); also elsewhere on the board
VIN: C17.1, C18.1, C19.1, C20.1, U2.21 (VS), U2.39 (VSA), U2.40 (VS); also elsewhere on the board

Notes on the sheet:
Copyright generationmake 2020 see full project documentation at https://github.com/generationmake/StepperMotorMKRShield
You may redistribute and modify this documentation under the terms of the CERN OHL v.1.2. (http://ohwr.org/cernohl). This documentation is distributed WITHOUT ANY EXPRESS OR IMPLIED WARRANTY, INCLUDING OF MERCHANTABILITY, SATISFACTORY QUALITY AND FITNESS FOR A PARTICULAR PURPOSE. Please see the CER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
use 2R2 if diode not installed
input voltage up to 46 V

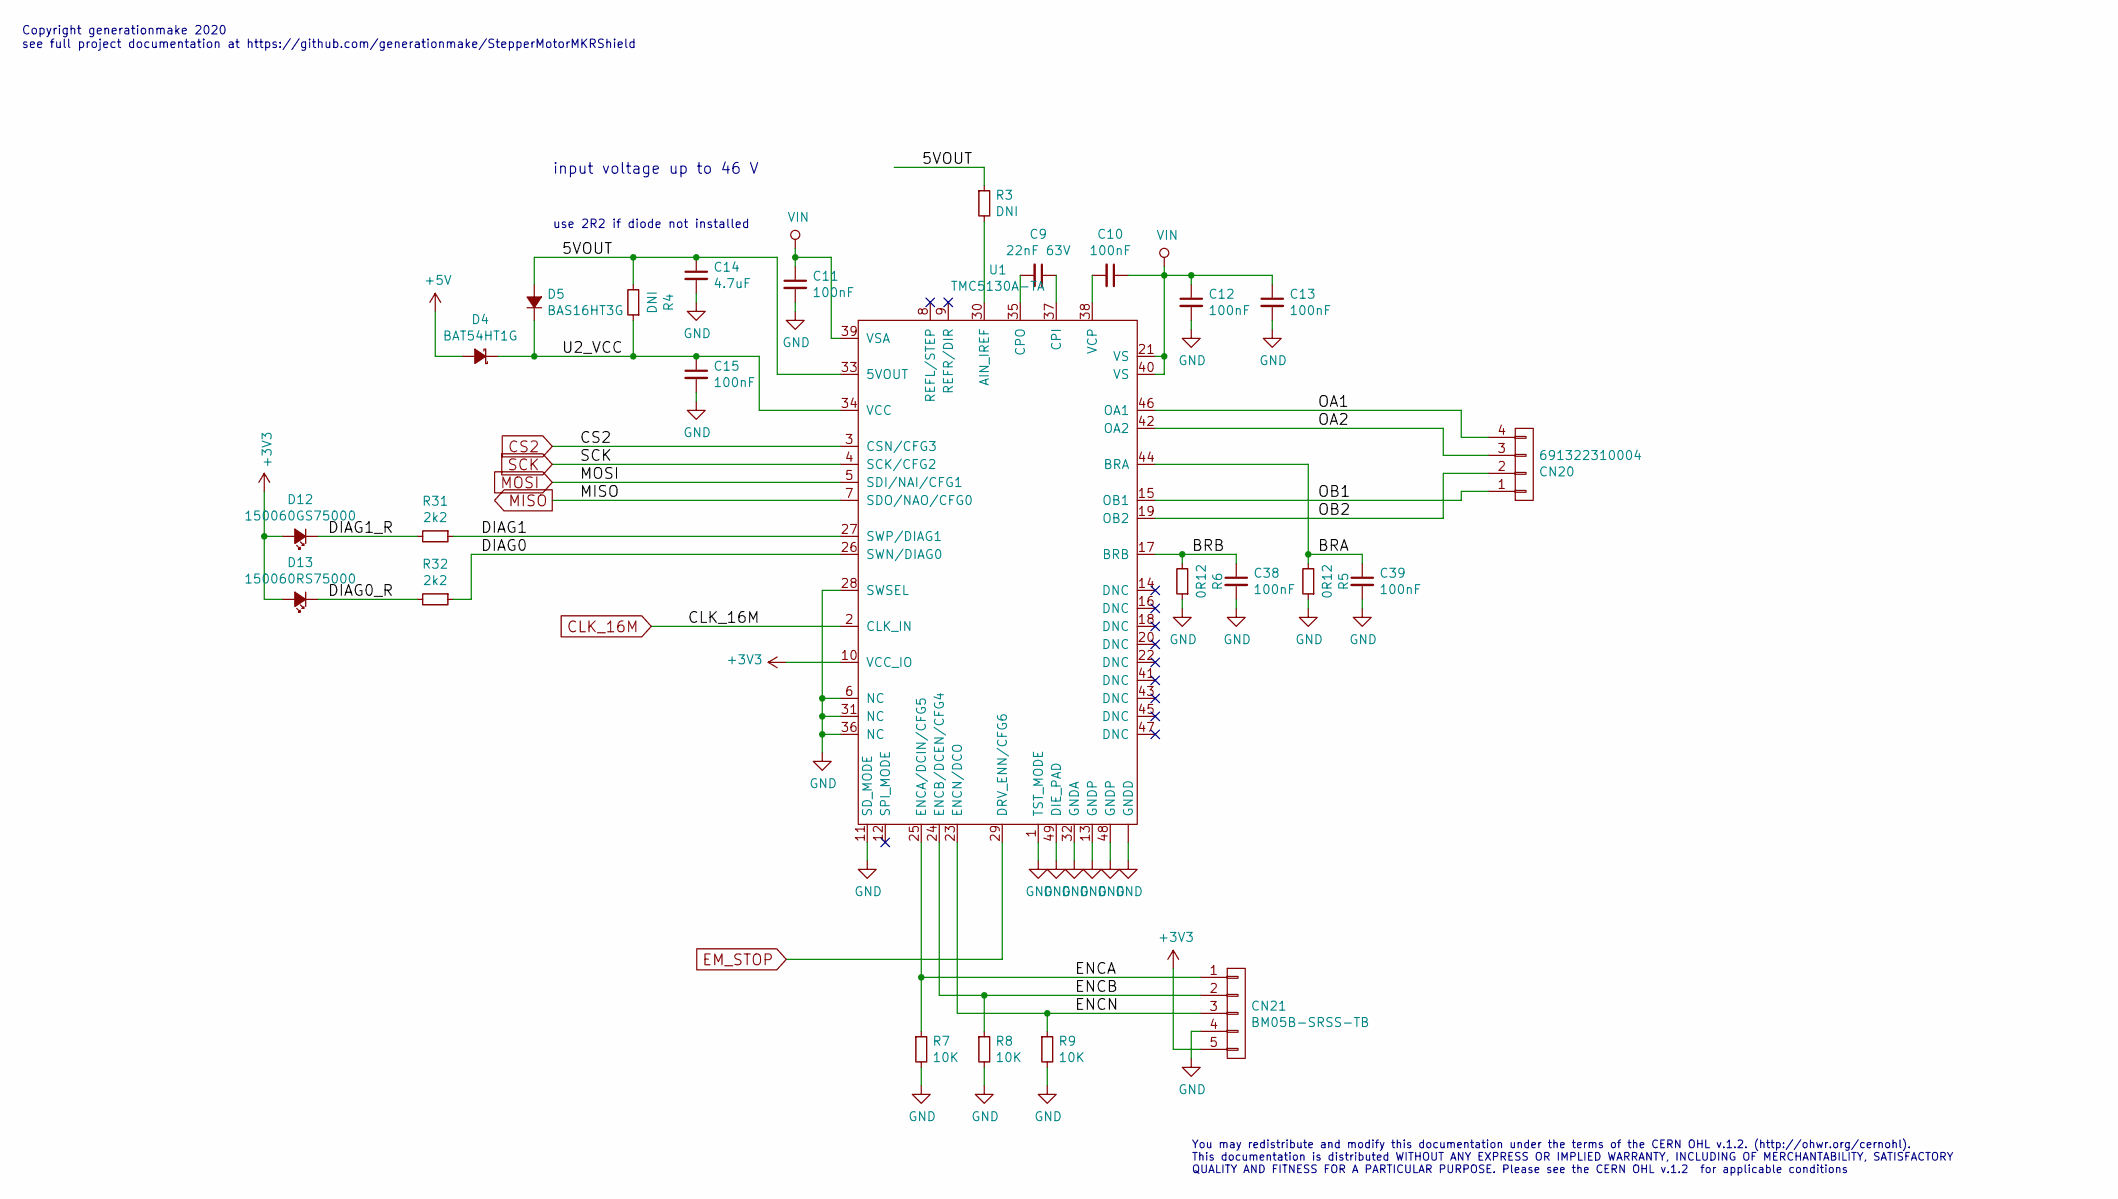
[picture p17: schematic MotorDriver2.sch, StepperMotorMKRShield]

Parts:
C9: 22nF 63V; C_0603
C10, C11, C12, C13, C15, C38, C39: 100nF; C_0603
C14: 4.7uF; C_0603
CN20: 691322310004; WR-TBL_691322310004
CN21: BM05B-SRSS-TB; Connectors_JST_BM05B-SRSS-TB
D4: BAT54HT1G; SOD-323
D5: BAS16HT3G; SOD-323
D12: 150060GS75000; LED_0603
D13: 150060RS75000; LED_0603
R3, R4: DNI; R_0603
R5, R6: 0R12; R_0805
R7, R8, R9: 10K; R_0603
R31, R32: 2k2; R_0603
U1: TMC5130A-TA; TQFP-48-1EP_7x7mm_Pitch0.5mm

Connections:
+3V3: CN21.5, D12.2 (A), D13.2 (A), U1.10 (VCC_IO); also elsewhere on the board
+5V: D4.2 (A); also elsewhere on the board
/MotorDriver2/5VOUT: C14.1, D5.2 (A), R3.1, R4.2, U1.33 (5VOUT)
/MotorDriver2/BRA: C39.1, R5.2, U1.44 (BRA)
/MotorDriver2/BRB: C38.1, R6.2, U1.17 (BRB)
/MotorDriver2/DIAG0: R32.1, U1.26 (SWN/DIAG0)
/MotorDriver2/DIAG0_R: D13.1 (K), R32.2
/MotorDriver2/DIAG1: R31.1, U1.27 (SWP/DIAG1)
/MotorDriver2/DIAG1_R: D12.1 (K), R31.2
/MotorDriver2/ENCA: CN21.1, R7.1, U1.25 (ENCA/DCIN/CFG5)
/MotorDriver2/ENCB: CN21.2, R8.1, U1.24 (ENCB/DCEN/CFG4)
/MotorDriver2/ENCN: CN21.3, R9.1, U1.23 (ENCN/DCO)
/MotorDriver2/OA1: CN20.4, U1.46 (OA1)
/MotorDriver2/OA2: CN20.3, U1.42 (OA2)
/MotorDriver2/OB1: CN20.1, U1.15 (OB1)
/MotorDriver2/OB2: CN20.2, U1.19 (OB2)
/MotorDriver2/U2_VCC: C15.1, D4.1 (K), D5.1 (K), R4.1, U1.34 (VCC)
CLK_16M: U1.2 (CLK_IN); also elsewhere on the board
CS2: U1.3 (CSN/CFG3); also elsewhere on the board
EM_STOP: U1.29 (DRV_ENN/CFG6); also elsewhere on the board
GND: C11.2, C12.2, C13.2, C14.2, C15.2, C38.2, C39.2, CN21.4, R5.1, R6.1, R7.2, R8.2, R9.2, U1.1 (TST_MODE), U1.6 (NC), U1.11 (SD_MODE), U1.13 (GNDP), U1.28 (SWSEL), U1.31 (NC), U1.32 (GNDA), U1.36 (NC), U1.48 (GNDP), U1.49 (DIE_PAD), U1.~ (GNDD); also elsewhere on the board
MISO: U1.7 (SDO/NAO/CFG0); also elsewhere on the board
MOSI: U1.5 (SDI/NAI/CFG1); also elsewhere on the board
unnamed: C9.1, U1.37 (CPI)
unnamed: C9.2, U1.35 (CPO)
unnamed: C10.2, U1.38 (VCP)
unnamed: R3.2, U1.30 (AIN_IREF)
SCK: U1.4 (SCK/CFG2); also elsewhere on the board
VIN: C10.1, C11.1, C12.1, C13.1, U1.21 (VS), U1.39 (VSA), U1.40 (VS); also elsewhere on the board

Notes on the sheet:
Copyright generationmake 2020 see full project documentation at https://github.com/generationmake/StepperMotorMKRShield
You may redistribute and modify this documentation under the terms of the CERN OHL v.1.2. (http://ohwr.org/cernohl). This documentation is distributed WITHOUT ANY EXPRESS OR IMPLIED WARRANTY, INCLUDING OF MERCHANTABILITY, SATISFACTORY QUALITY AND FITNESS FOR A PARTICULAR PURPOSE. Please see the CER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
use 2R2 if diode not installed
input voltage up to 46 V

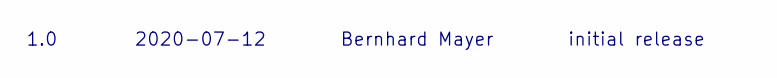
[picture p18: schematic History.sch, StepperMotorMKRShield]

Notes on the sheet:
1.0
2020-07-12
Bernhard Mayer
initial release

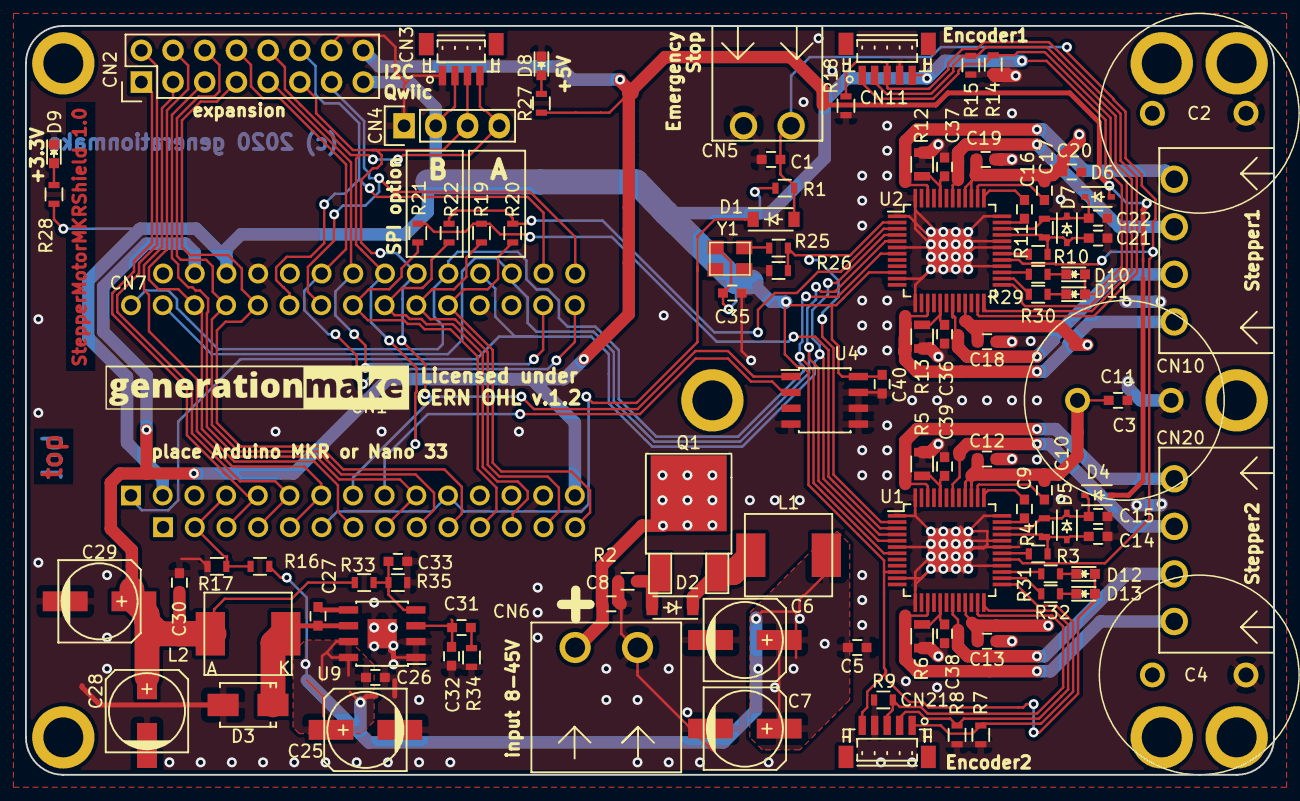
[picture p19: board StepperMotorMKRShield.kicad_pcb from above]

Board: 2 copper layers, 100.0 x 60.0 mm, 112 parts (0 on the bottom side), 79 nets.

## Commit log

2019-12-31 added kicad source
    [History.sch, Measurement.sch, MotorDriver1.sch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]
2019-12-31 generated pdf files
    [History.sch, Measurement.sch, MotorDriver1.sch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]
2020-01-01 added mounting instructions
    [StepperMotorFeatherWing.kicad_pcb]
2020-04-16 added most missing 3d models, changed mounting holes to parts and generated step model
    [StepperMotorFeatherWing.kicad_pcb, VoltageRegulator.sch]
2020-07-03 added external supply for +5V for TMC5130
    [History.sch, MotorDriver1.sch, MotorDriver2.sch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]
2020-07-03 added clock generator as common clock for both stepper drivers
    [History.sch, MotorDriver1.sch, MotorDriver2.sch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]
2020-07-04 added leds and decoupling capacitors
    [History.sch, Measurement.sch, MotorDriver1.sch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]
2020-07-04 changed type of encoder connector
    [MotorDriver1.sch, MotorDriver2.sch, StepperMotorFeatherWing.kicad_pcb]
2020-07-05 added temperature sensor LM75
    [History.sch, Measurement.sch, StepperMotorFeatherWing.kicad_pcb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]
2020-07-06 updated layout
    [History.sch, Measurement.sch, MotorDriver1.sch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]
2020-07-07 update layout
    [StepperMotorFeatherWing.kicad_pcb]
2020-07-07 added expansion connector, updated layout
    [History.sch, Measurement.sch, MotorDriver1.sch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]
2020-07-07 added pdf schematic and renderings
2020-07-08 updated part numbers
    [Measurement.sch, MotorDriver1.sch, MotorDriver2.sch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]
2020-07-11 corrected position of mounting holes for heat spreader, added information on input voltage
    [History.sch, MotorDriver1.sch, MotorDriver2.sch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]
2020-07-11 changed L1 and L2 to Sumida 0624CDMCCDS for better availability
    [History.sch, StepperMotorFeatherWing.kicad_pcb, VoltageRegulator.sch]
2020-07-11 corrected order numbers of capacitors
    [StepperMotorFeatherWing.kicad_pcb, VoltageRegulator.sch]
2020-07-11 updated pdf files
    [History.sch, Measurement.sch, MotorDriver1.sch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]
2020-07-11 renamed all files to new project name
    [StepperMotorMKRShield.kicad_pcb, StepperMotorMKRShield.sch, StepperMotorMKRShield.xml]
2020-07-11 added CN1 from adafruit feather to arduino MKR
    [Measurement.sch, StepperMotorMKRShield.sch, VoltageRegulator.sch]
2020-07-11 removed regulator for 5V external
    [VoltageRegulator.sch]
2020-07-11 corrected links and titles, generated schematic pdf and net list
    [History.sch, Measurement.sch, MotorDriver1.sch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]
2020-07-12 added Arduino Nano 33 header in schematic
    [StepperMotorMKRShield.kicad_pcb, StepperMotorMKRShield.sch]
2020-07-12 replaced tantal capacitors with aluminium-electronlytic capacitors with higher voltage to allow up to 45 V on input
    [StepperMotorMKRShield.kicad_pcb, VoltageRegulator.sch]
2020-07-13 generated pdf schematic

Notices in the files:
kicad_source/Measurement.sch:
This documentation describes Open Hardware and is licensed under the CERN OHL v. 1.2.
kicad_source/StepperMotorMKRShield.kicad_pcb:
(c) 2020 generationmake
